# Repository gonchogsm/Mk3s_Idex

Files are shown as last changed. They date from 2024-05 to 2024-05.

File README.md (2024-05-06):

# Mk3s Idex

This project was born to try and learn about Idex printers. I had a Prusa Mk3s printer so I modified the X carriage to add a second extruder.

This is not a finished project and some work is needed to have a fully functional Idex printer. Please refer to the "To-do" section and use at your own risk.





## What do you need
### Hardware
- Prusa Mk3s.
- Raspberry Pi. To run klipper.
- Nema17 motor with pulley. To move the extra extruder in the X axis.
- Complete Mk3s extruder. Motor, gears, fans, hotend, etc.
- Board to run the extra extruder and X motor. I used a SKR Pico that I already had but any other board should work as well.
- 24v power supply. I used a 200W 24v power supply to power the SKR Pico as I didn't want to mess with the original power supply.
- 2x GT2 16T pulley https://es.aliexpress.com/item/32817328238.html (16T W6 B3 without T).
- Linear rail 350mm. If you use a wider frame, remember to buy a longer linear rail.
- 2x carriage block MGN12H.
- GT2 belt for second extruder.
- POM nuts and linear bearings from old X axis.
> [!WARNING]
> Remember to check fan voltage! Original Prusa fans run at 5v but your additional board (i.e. SKR Pico) will run at 12 or 24v.

#### Screws (socket head if not specified)
##### X axis
- 2x M3x25 (tensioner)
- 2x M3 nut (tensioner)
- 2x M3x14 pin (to hold tensioner pulley)
- 3x M3x10 (to hold left motor)
- 3x M3x12 (to hold right motor)
- 4x M3x10 (Z rod clamps)
- 4x M3x18 (POM nuts)
- 8x M3 nuts
##### Tool backplate
- 1x M3x8
- 2x M3x10
- 1x M3x16
- 4x M3 nuts
##### Tool carriage
- 8x M3x6 countersunk head
##### Extruder 1
- Screws and nuts to mount the second extruder. Please refer to Prusa documentation.

#### Frame
> [!CAUTION]
> Using stock frame will leave one or both nozzles on top of the bed when extruders are parked. You must ensure that first layers are ALWAYS done with the extruder that sits at a lower height. Otherwise the other nozzle will scratch your bed surface. I recommend using a wider frame, where both extruders are parked outside the bed, to overcome this issue. Please refer to the "To-do" section.

### Printed parts
#### X axis
- x-axis-idler Idex.stl
- x-axis-motor-mount Idex.stl
- x-end-idler-tensioner x2.stl
#### Tool 0
- x-carriage Idex Tool 0.stl
- x-carriage-back Idex Tool 0.stl
#### Tool 1
- x-carriage Idex Tool 1.stl
- x-carriage-back Idex Tool 1.stl
- Print original Mk3s extruder parts. Except x-carriage and x-carriage-back.

## Firmware
I recommend starting with a Prusa Mk3s running Klipper via [RatOS](https://os.ratrig.com/).

Once everything works and you have calibrated pid, skew, etc you can add the second extruder.

You can use the provided printer.cfg with the configuration needed for the second extruder.

## Slicer
Import "PrusaSlicer config.ini" configuration into PrusaSlicer.

## Tool alignment
Tools can be aligned using a camera [kTAMV](https://github.com/TypQxQ/kTAMV) or using [printed patterns](https://www.printables.com/model/129617-offset-xy-dual-extruder-idex-calibration)

## To-Do
### Endstops
I noticed inconsistent home positions when homing X. It could be an issue with sensorless homing or with my configuration. It would be worth trying physical endstops in X for both extruders.
### Z endstop in second extruder
Pinda probe configuration in the second extruder is pending.
### Frame
With stock frame you can't use all the bed. The frame should be replaced with a Prusa Bear frame but wider in X so both extruders are parked outside the bed. Note that each extruder is aprox 8cm wide, so the frame should be, at least, 16cm wider in X. Maybe extra 20cm in X?
### Extruders
- Add a resting pad for each extruder to prevent oozing when parked.
- One extruder may be mirrored to increase clearance between extruders
### Electronics
An alternative to use an additional board (i.e. SKR Pico), would be to use an EBB36 board in each extruder. Each board will control one extruder and they will be connected to the raspberry Pi via USB. That will free one stepper in the einsy board that can be used to control the extra X motor.
### Mirror and copy mode
Both hotends must be at the same Z height to use mirror or copy mode. This has to be achieved by hardware. One solution is to use [Slice Engineering copperhead hotend](https://www.sliceengineering.com/collections/copperhead) in both extruders. This hotend allows you to set the heat breaks at a different height as it's not a threaded heat breaks, it's secured in place by a screw. The idea is to loose both heat breaks, push both nozzles into the bed, then tighten the screws in both hotends to secure the heat breaks.

## Credits
CM3D MK3S: https://github.com/ComunidadMaker3D/CM3D-MK3S

MK3 Caribou3D: https://github.com/Caribou3d/Caribou-MK3

Prusa Research: http://prusa3d.com

Prusa MK3s+ Lineal Rails X axis (Bear Project and CM3D remixed): https://www.printables.com/model/616378-prusa-mk3s-lineal-rails-x-axis-bear-project-and-cm

## Warning
This is a work in progress. Use at your own risk ;-).

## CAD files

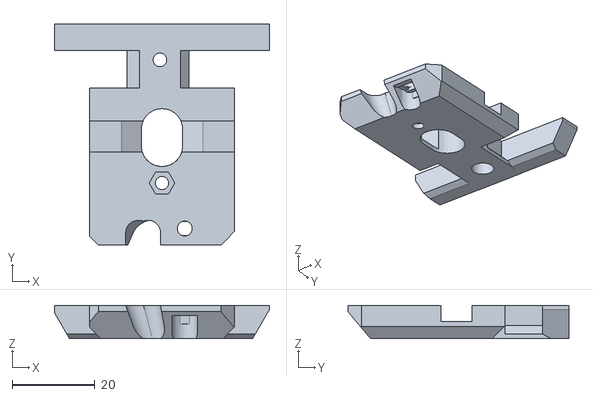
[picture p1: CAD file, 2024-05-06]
STL/x-carriage-back Idex Tool 0.stl
52.0 x 53.5 x 8.00

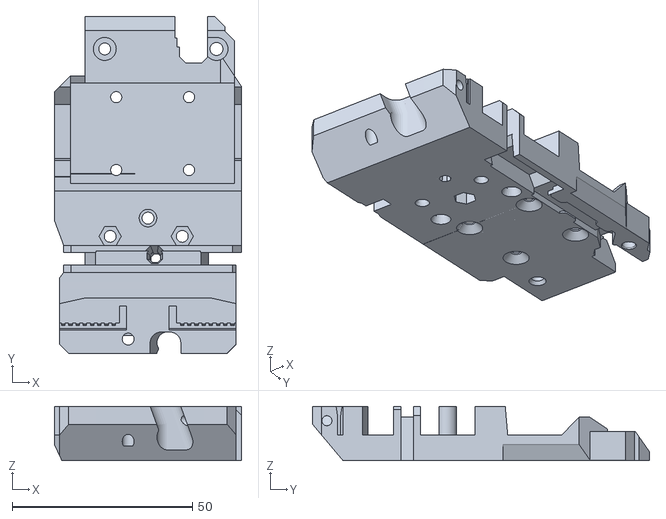
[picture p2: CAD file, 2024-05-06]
STL/x-carriage Idex Tool 1.stl
52.0 x 93.5 x 15.1

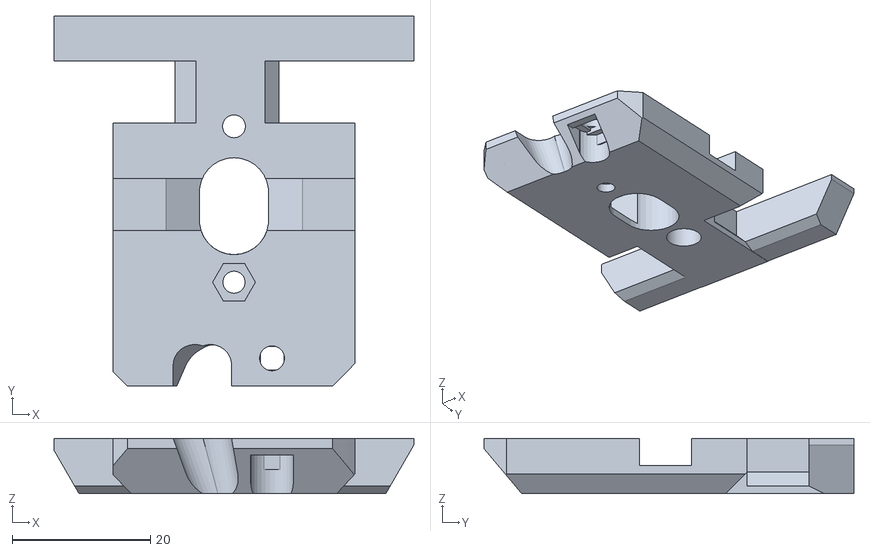
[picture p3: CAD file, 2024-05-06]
STL/x-carriage-back Idex Tool 1.stl
52.0 x 53.5 x 8.00

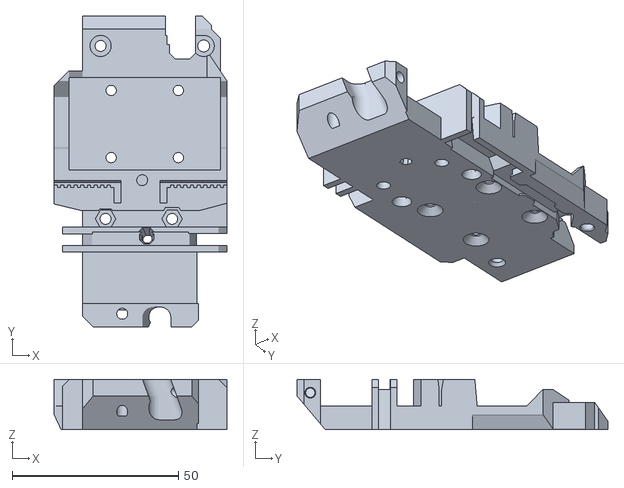
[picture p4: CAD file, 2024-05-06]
STL/x-carriage Idex Tool 0.stl
52.0 x 93.5 x 15.1

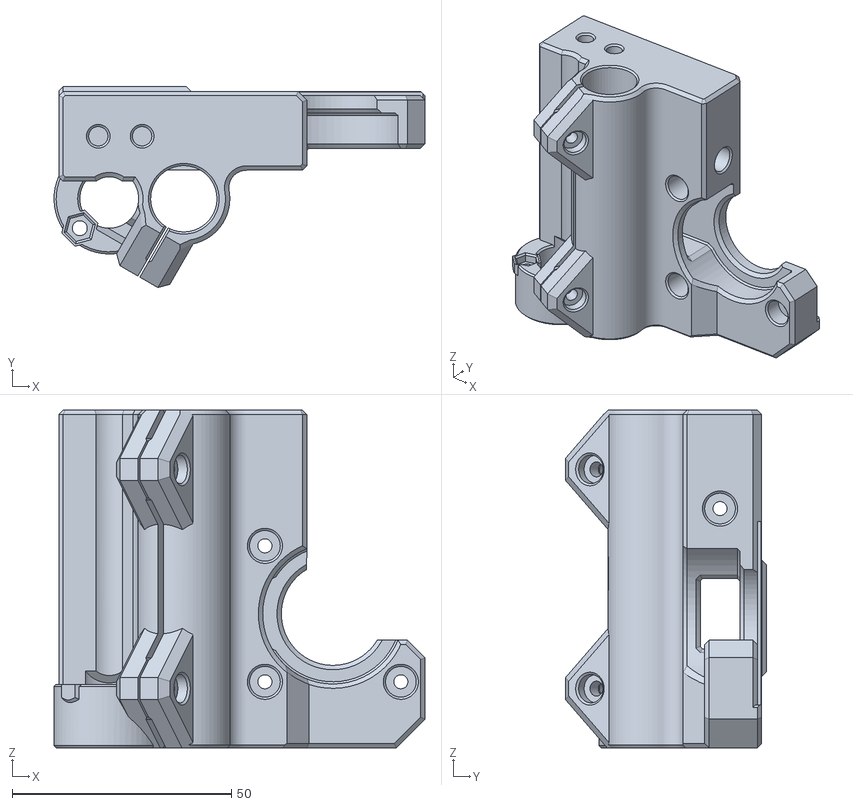
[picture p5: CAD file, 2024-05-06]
STL/x-axis-motor-mount Idex.stl
84.6 x 45.9 x 77.0

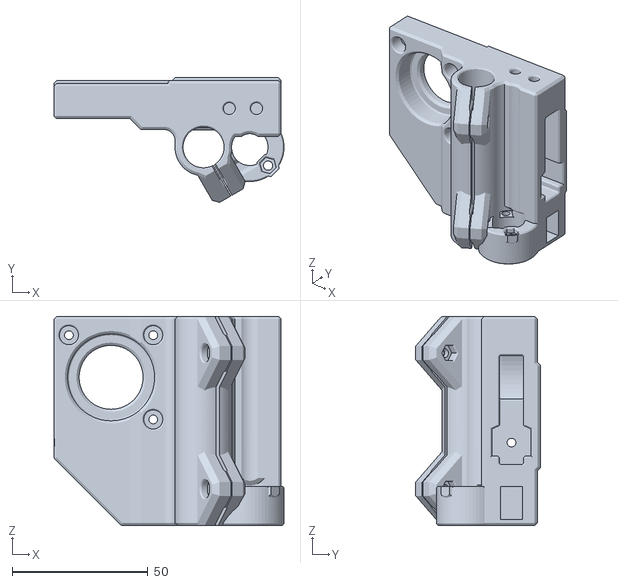
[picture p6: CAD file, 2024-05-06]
STL/x-axis-idler Idex.stl
84.6 x 45.9 x 77.0

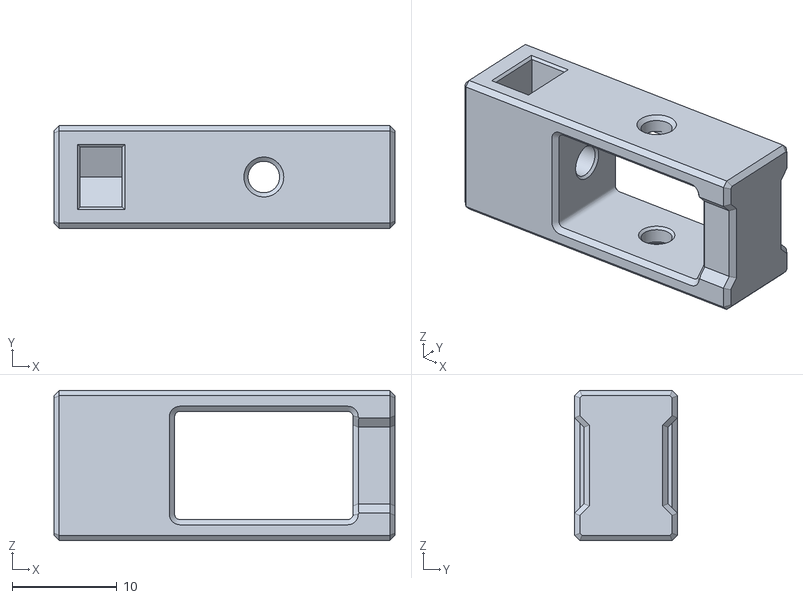
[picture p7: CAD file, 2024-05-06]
STL/x-end-idler-tensioner x2.stl
32.5 x 9.80 x 14.3

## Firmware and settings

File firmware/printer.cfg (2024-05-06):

# Prusa MK3S RatOS config file
# Documentation: https://os.ratrig.com

# The first thing you'll need to do is go through this file and comment out / uncomment
# the files and/or settings you need.
# You'll be able to print just fine with this config as it is, but it is recommended
# that you follow these steps to properly calibrate your printer:
# 0) Sanity check and PID Tuning: https://www.klipper3d.org/Config_checks.html
# 1) Pressure Advance: https://www.klipper3d.org/Pressure_Advance.html
# 2) Skew Correction: https://www.klipper3d.org/Skew_Correction.html
# 3) Resonance Compensation: https://www.klipper3d.org/Resonance_Compensation.html

# Read more about klipper here: https://www.klipper3d.org/Overview.html

#############################################################################################################
### CONTROL BOARD
### Pick the board you have installed and wired in your printer.
#############################################################################################################
[include RatOS/boards/prusa-einsy/config.cfg]
#[include RatOS/boards/btt-skr-2-429/config.cfg]
#[include RatOS/boards/btt-octopus-11/config.cfg]
#[include RatOS/boards/btt-octopus-11-407/config.cfg]
#[include RatOS/boards/btt-octopus-max-ez/config.cfg]
#[include RatOS/boards/btt-octopus-pro-429/config.cfg]
#[include RatOS/boards/btt-octopus-pro-446/config.cfg]
#[include RatOS/boards/btt-manta-m8p/config.cfg]
#[include RatOS/boards/btt-manta-m8p-11/config.cfg]
#[include RatOS/boards/btt-skr-pro-12/config.cfg]
#[include RatOS/boards/fysetc-spider/config.cfg]

### RPI Mcu (Necessary for dual sensor input shaping)
#[include RatOS/boards/rpi/config.cfg]


#############################################################################################################
### BASE SETUP
#############################################################################################################
[include RatOS/printers/prusa-mk3s/prusa-mk3s.cfg]
[include RatOS/homing.cfg]
[include RatOS/macros.cfg]
[include RatOS/shell-macros.cfg]
[include RatOS/printers/prusa-mk3s/macros.cfg]


#############################################################################################################
### STEPPER MOTORS, DRIVERS & SPEED LIMITS
### Pick the drivers and stepper motors you're using. See the RatOS documentation for custom combinations.
#############################################################################################################
[include RatOS/printers/prusa-mk3s/steppers.cfg]

# UNCOOLED TMC 2130 + LDO-42STH40-1684AC
# It is recommended that you enable these settings until you have verified that your printer moves as expected
[include RatOS/printers/prusa-mk3s/tmc2130.cfg]
[include RatOS/printers/prusa-mk3s/speed-limits-basic.cfg]
[include RatOS/steppers/ldo/42sth40-1684ac/2130/24v-0.4a-*.cfg]

# STEALTH MODE
# NOTE: You still need to include one of the above stepper motor definitions.
# NOTE: This will make your printer quiter but less accurate, it's an inherent side effect of stealthchop.
# NOTE: This will also impact your acceleration and print speed significantly.
#[include RatOS/printers/prusa-mk3s/tmc2130-stealth.cfg]


#############################################################################################################
### HOMING
### Pick your probe and endstops
#############################################################################################################
# BL Touch
#[include RatOS/z-probe/bltouch.cfg]
# Inductive/Capacitive probe
[include RatOS/z-probe/probe.cfg]

# Physical endstops
# Sensorless homing (Beware: this requires manual tinkering and does not work if your x/y stepper drivers
# have clipped DIAG pins). It is strongly encouraged to use physical endstops if you're a beginner.
# If you still wish to proceed, copy RatOS/templates/sensorless-homing.cfg to the root directory and
# remove the # from the line below.
[include RatOS/printers/prusa-mk3s/sensorless-homing-tmc2130.cfg]
[include RatOS/homing.cfg]


#############################################################################################################
### INPUT SHAPER
### Enable/disable input shaper calibration
#############################################################################################################
# Uncomment the following line to use a single ADXL345 that you manually move between
# the X and Y axis. (Use SHAPER_CALIBRATE AXIS=X and SHAPER_CALIBRATE AXIS=Y respectively).
# The ADXL345 should be connected to your Raspberry Pi. See the wiring instructions here:
# https://www.klipper3d.org/Measuring_Resonances.html
# NOTE: You ONLY need to wire the ADXL345, everything else is already done for you.
#[include RatOS/printers/prusa-mini/input-shaper-single.cfg]

# Alternatively check https://www.klipper3d.org/Resonance_Compensation.html for manual input shaper calibration.


#############################################################################################################
### TOOLHEAD
### Pick your extruder and hotend
#############################################################################################################
# Extruder
[include RatOS/extruders/mk3s.cfg]
#[include RatOS/extruders/tl-31.cfg]
#[include RatOS/extruders/prusa-mini.cfg]
#[include RatOS/extruders/lgx-lite.cfg]
#[include RatOS/extruders/bmg.cfg]
#[include RatOS/extruders/lgx.cfg]
#[include RatOS/extruders/orbiter.cfg]
#[include RatOS/extruders/orbiter-1004.cfg] # Use this with the LDO-36STH20-1004AHG motor
#[include RatOS/extruders/hemera.cfg]
#[include RatOS/extruders/titan.cfg]

# Hotend
#[include RatOS/hotends/dragonfly.cfg]
#[include RatOS/hotends/rapido.cfg]
[include RatOS/hotends/v6.cfg]
#[include RatOS/hotends/revo.cfg]
#[include RatOS/hotends/copperhead.cfg]
#[include RatOS/hotends/mosquito.cfg]
#[include RatOS/hotends/mosquito-magnum.cfg]
#[include RatOS/hotends/dragon-standard-flow.cfg]
#[include RatOS/hotends/dragon-high-flow.cfg]


#############################################################################################################
### LCD
### Pick your LCD configuration
#############################################################################################################
[include RatOS/printers/prusa-mk3s/display.cfg]


#############################################################################################################
### FILAMENT SENSOR
### Pick your filament sensor configuration
#############################################################################################################
#[include RatOS/sensors/prusa-mk3s-filament-switch.cfg]
# Disable automatic filament loading for now
[filament_switch_sensor filament_sensor]
switch_pin: !filament_switch_sensor_pin
pause_on_runout: True
runout_gcode:
    M118 Filament Runout Detected
    M600
insert_gcode:
    M118 Filament Load Detected
    #LOAD_FILAMENT
event_delay: 3.0
pause_delay: 0.01


#############################################################################################################
### FANS
### Pick your fan configuration
#############################################################################################################
[include RatOS/4pin-fans/toolhead-fan-100hz.cfg]
#[include RatOS/4pin-fans/part-cooling-fan-100hz.cfg]
[fan_generic fan]
pin: 4p_fan_part_cooling_pin
tachometer_pin: ^4p_fan_part_cooling_tach_pin 
tachometer_poll_interval: 0.0005
cycle_time: 0.01



#############################################################################################################
### MACRO CONFIGURATION
### Configure the behavior of RatOS macros
### See: https://os.ratrig.com/docs/configuration/macros
#############################################################################################################
[gcode_macro RatOS]
variable_relative_extrusion: False
variable_preheat_extruder: True
variable_calibrate_bed_mesh: True
variable_nozzle_priming: "primeblob"
variable_nozzle_prime_start_x: 2
variable_start_print_park_in: "front"
variable_start_print_park_z_height: 50
variable_end_print_park_in: "back"
variable_pause_print_park_in: "front"
variable_macro_travel_speed: 200
variable_filament_unload_length: 100
variable_filament_unload_speed: 5
variable_filament_load_length: 100
variable_filament_load_speed: 10
variable_driver_type_x: "tmc2130"
variable_driver_type_y: "tmc2130"
variable_end_print_park_x: 150


#############################################################################################################
### PRINTER CONFIGURATION
### Customize the defaults to your specific build
#############################################################################################################
[tmc2130 extruder]
sense_resistor: 0.22

[extruder]
pressure_advance: 0.04 #this is a reference value, should be calibrated on each printer
#control = pid
#pid_Kp: 16.13
#pid_Ki: 1.1625
#pid_Kd: 56.23

[heater_bed]
#control = pid
#pid_Kp: 126.13
#pid_Ki: 4.3
#pid_Kd: 924.76
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
